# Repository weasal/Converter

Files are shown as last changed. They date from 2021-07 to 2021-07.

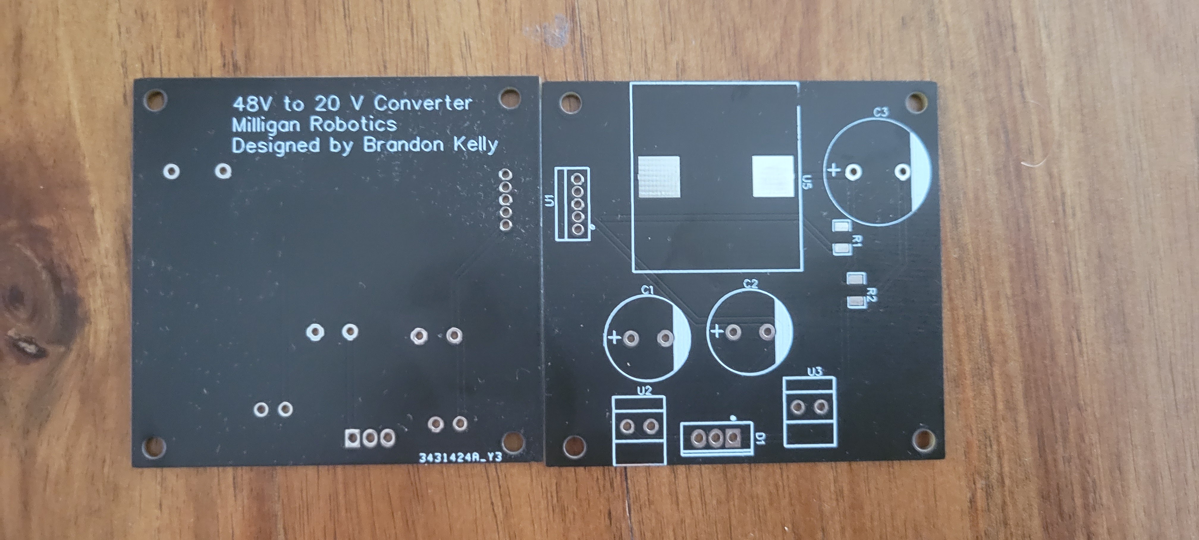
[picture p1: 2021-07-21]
20210721_164908.jpg

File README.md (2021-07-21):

# Converter
A DC-DC converter built around the TI LM2576.  Designed for use in the MATE Robotics competition in order to convert 48 Volts to necessary voltages. 
# Purpose
For the MATE robotics Explorer Category, we needed to deal with a 48V power supply.  As most of our electronics were not compatible with this voltage, we needed to convert it into something we could use.  The voltages required were primarily 18V for our thrusters and 5V and 12V for various electronics and servos.  Due to certain restrictions on how we could handle this conversion, size, efficiency, and simplicity were key concerns.  Because of this, I elected to go with a switching power supply, specifically a buck converter, which allowed for high efficiency and widespread and available documentation.  While there was an option to build a more fundamental design, both ease of assembly and availability of documentation drove me to use a Texas Instruments IC.  While the practical purpose was paramount, I also took the opportunity to educate myself about converter topology, board layout best practices, and PCB design tools. 
# Design Process
As I had never designed something like this, the first place I started was researching the theory and principles of power conversion.  After gaining a better grasp of the mechanics of the converter, I used the Texas Instruments WEBENCH tool to pick the IC to power the converter and pick the passive components.  I then used EasyEDA to design the layout and generate Gerber files.
# Key Features
1. Low Cost
2. Simple assembly with minimal SMT Components
3. Relatively small dimensions
4. Easy connections
# Implantation and Retrospective.
Due to time and COVID restraints, we were unable to validate and test the design.  We elected to go with other methods due to difficulty obtaining certain components and in order to decrease the amount of time building, testing, and debugging our electrical system.  I was able to procure PCBs and do basic continuity checks to ensure that the device had all connections routed correctly. Looking back at the design process, some compromises were made that I would like to rectify in a redesign.  Most notable of these was the inductor I had designed for was simply too big for us to fit more than a couple in our space.  While this was not a deal-breaker from a general use perspective, this fact coupled with a relatively low max current supported by the IC and more significant than expected power demand for our ROV left this solution inadequate for powering the entire ROV.  The other major concern I have with the current design is the board layout I had created.  While everything should work as expected, there are some problems.  One is the lack of pre-planned or standard size, meaning that any enclosure or support structure would have to be completely custom-designed.  Related to this was space wasted that likely could have been removed with better placement of various components.  The last major issue I would fix is the silkscreen.  While the components, VIN pin, and capacitor polarities are marked on the board, there are definitely some problem areas I would fix, most notably the lack of notation near the input and output terminals (While the documentation I created does include enough information to assemble and wire the device correctly, it is not as user friendly as it could be).  While not an inherent flaw, I would likely not make the same compromises involving THT components, as there could have been significant space savings at the cost of ease-of-assembly if more SMT components had been used. Overall, I am proud of the work I have done on the project and look forward to iterating and improving.

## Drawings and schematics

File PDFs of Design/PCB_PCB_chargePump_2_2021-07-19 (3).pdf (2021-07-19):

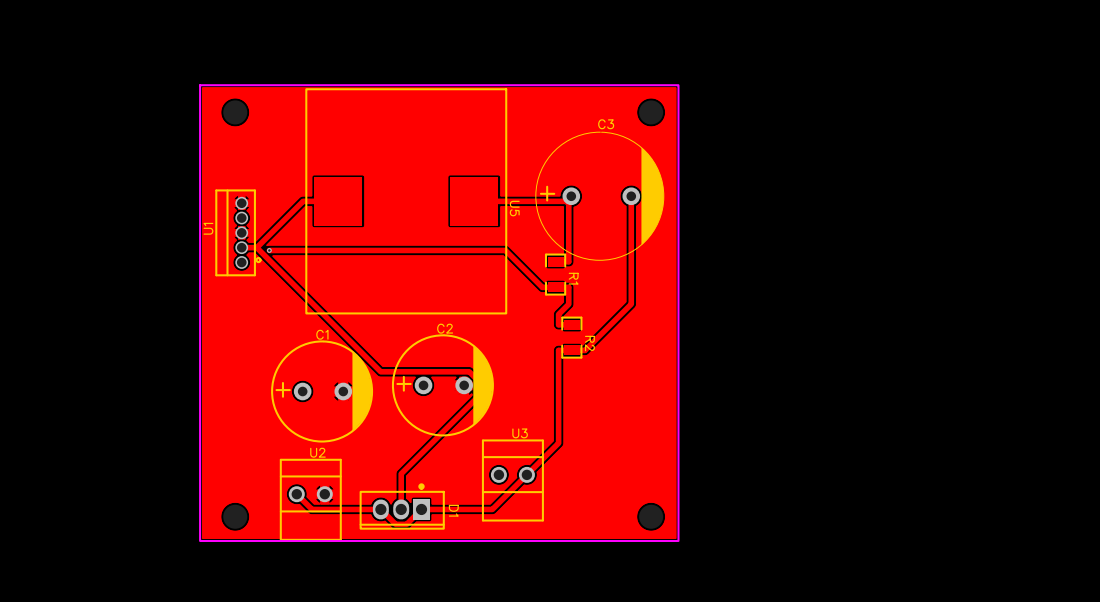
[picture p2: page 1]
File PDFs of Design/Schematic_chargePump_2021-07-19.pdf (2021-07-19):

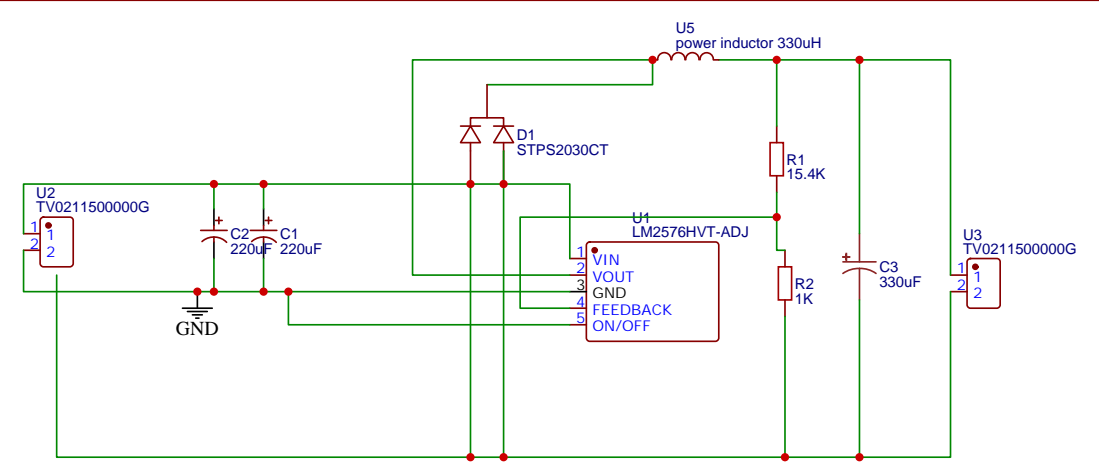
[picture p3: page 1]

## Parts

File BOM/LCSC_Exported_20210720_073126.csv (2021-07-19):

LCSC Part Number | Manufacture Part Number | Manufacturer | Package | Customer # | Description | RoHS | Order Qty. | Min\Mult Order Qty. | Unit Price | Order Price | Product Link
C59392 | KM221M100I200A | Capxon International Elec | 径向引线,13x20mm |  | 径向引线,13x20mm Aluminum Electrolytic Capacitors - Leaded ROHS | yes | 10 | 1 | 0.193 | - | https://assets.lcsc.com/images/lcsc/96x96/20190428_Capxon-International-Elec-KM221M100I200A_C59392_front.jpg
C116510 | ERF1KM331L20OT | AISHI(Aihua Group) | 径向引线,16x20mm |  | 径向引线,16x20mm Aluminum Electrolytic Capacitors - Leaded ROHS | yes | 3 | 1 | 0.4707 | - | https://assets.lcsc.com/images/lcsc/96x96/20180914_AISHI-Aihua-Group-ERF1KM331L20OT_C116510_front_10.jpg
C171654 | STPS2030CT | STMicroelectronics | TO-220(TO-220-3) |  | TO-220(TO-220-3) Schottky Barrier Diodes (SBD) ROHS | yes | 4 | 1 | 0.6835 | - | https://assets.lcsc.com/images/lcsc/96x96/20180914_STMicroelectronics-STPS2030CT_C171654_front.jpg
C246639 | RTT061542FTP | RALEC | 1206 |  | 1206 Chip Resistor - Surface Mount ROHS | yes | 50 | 50 | 0.0086 | - | https://assets.lcsc.com/images/lcsc/96x96/20180914_RALEC-RTT061542FTP_C246639_front.jpg
C328410 | AECR1206F1K00K9 | Resistor.Today | 1206 |  | 1206 Chip Resistor - Surface Mount ROHS | yes | 50 | 50 | 0.007 | - | https://assets.lcsc.com/images/lcsc/96x96/20181115_Resistor-Today-AECR1206F1K00K9_C328410_front.jpg
C126041 | LM2576HVT-ADJ | HTC Korea TAEJIN Tech | TO-220-5 |  | TO-220-5 DC-DC Converters ROHS | yes | 5 | 1 | 1.6951 | - | https://assets.lcsc.com/images/lcsc/96x96/20180914_HTC-Korea-TAEJIN-Tech-LM2576HVT-ADJ_C126041_front.jpg
C2683163 | TV0211500000G | Amphenol ICC | P=3.5mm |  | P=3.5mm Screw terminal ROHS | yes | 10 | 1 | 0.5176 | - | https://assets.lcsc.com/images/lcsc/96x96/20210323_Amphenol-ICC-TV0211500000G_C2683163_front.jpg
